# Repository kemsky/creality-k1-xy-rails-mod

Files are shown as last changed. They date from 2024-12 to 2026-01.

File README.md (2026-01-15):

# Creality `K1` XY Rails Mod

## Description

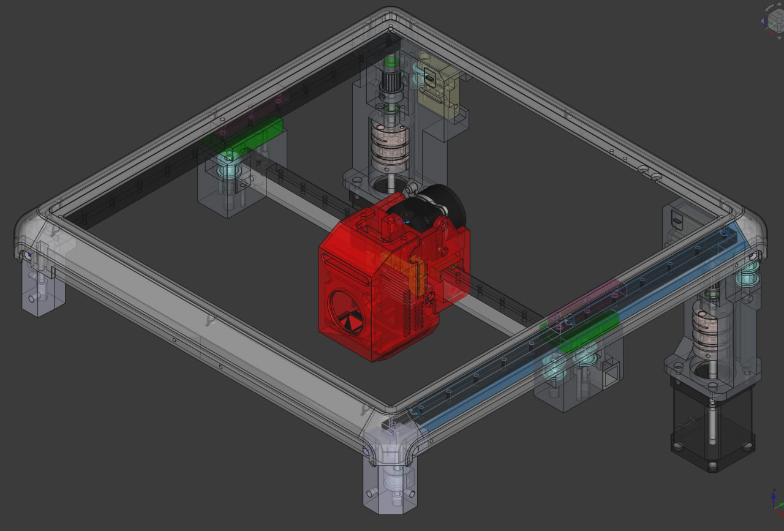
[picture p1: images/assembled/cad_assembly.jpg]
CAD


This mod fixes `K1` issues namely excessive ringing/echo, unstable print quality, frequent maintenance, also it makes printer quiet.

It should be compatible with regular `K1` (tested), `K1C` and `K1 SE` (not tested, likely heat sink needs to be replaced with heatsink from regular `K1`).

- **This mod does not change print area**
- **You must use camera mount from this mod (8mm lower than original)**
- **You must remove stock motor pulleys (or use non-stock stepper motors)**

### Belts, pulleys, motors

This mode uses `POWGE` 7.7 mm belt and corresponding idler pulleys. You can use 6 mm belt and stock idlers if you add washers to compensate height differences (`POWGE` idlers have 10.4 mm height). Also, you can use `F604ZZ` flanged bearings (4x12x4) and 2mm washers instead of `POWGE` pulleys.

You have to remove stock motor pulleys. You can use a bearing puller to do that (some people use printed pullers e.g. [pulley puller](https://www.printables.com/model/515503-pulley-puller)). If pulleys sit too tight you can use dremel and make cuts to relax pulleys. you have to be careful to avoid damage to motor shafts

I used 20T motor pulleys for 15 mm belt (`rotation_distance` needs to be adjusted to `40` and `driver_SGTHRS` must be tuned `printer.cfg`).

You can install non-stock motors e.g. `Leadshine 42cm06 1.8` (low VFA, need custom wiring, expensive) or `LDO-42STH48-1684MAC 0.9` (requires `full_steps_per_rotation: 400`, loud, limited acceleration, low VFA).

This mod uses double diaphragm couplers and `MF95ZZ` bearings.

#### Belts tuning

Preferred way is to use Spectroid android app (or any other program that can show sound frequency).

Move toolhead to the middle, move X axis to have 150mm between motor mounts and XY joints.

Pluck the shortest belt on each side, displayed frequency should be the same. Target frequency is 120-130Hz, if you go higher than 130Hz you risk to damage belts.

#### Linear rails

This mod uses two `MGN12` rails with `MGN12H` carriages for Y and one `MGN9` rail with `MGN9H` carriage for X axis.

X rail has max length of 331 mm, 300 mm between far left and far right holes. X axis requires 15x15x2 mm aluminium tube (the same length as rail). It is important to use quality rails for X axis (with minimal backlash).

Y rails have max length of 314 mm (safe 310 mm), 300 mm between far left and far right holes.

#### Materials

Recommended printing materials are PA-GF, PA-CF, ABS-GF, ABS-CF or anything else that is rigid and can sustain high temperatures. I don't recommend printing toolhead with pure ABS. I'd recommend PA-GF or PA-CF, as screw joints tend to become loose in ABS.

Wall loops, top/bottom layers should be at least 5, for motor mounts I'd recommend 6-7.

<details>
    <summary>Printing orientation</summary>
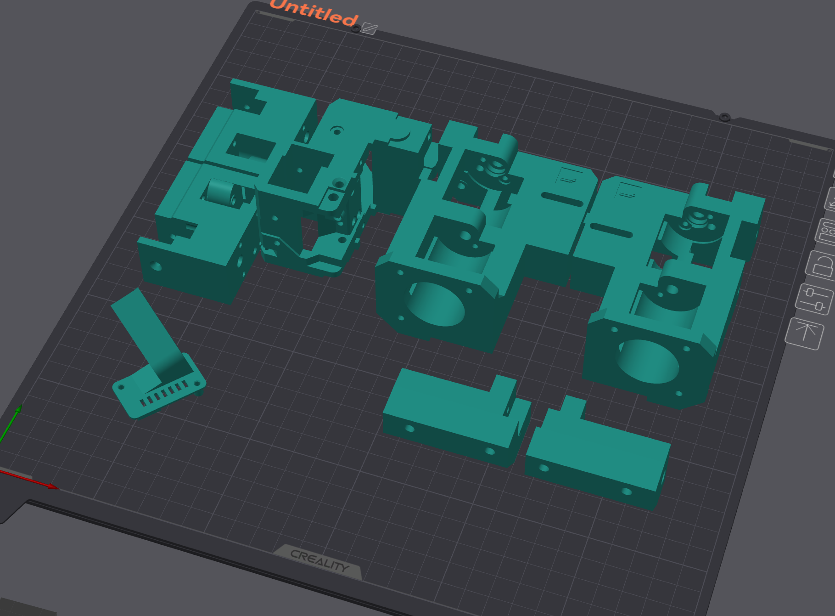
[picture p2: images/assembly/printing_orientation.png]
    
</details>

#### Options for maximum performance

- Use light extruder - [KKm extruder](https://www.printables.com/model/906070-artis3d-kkm-extruder-remix) (probably I'll upload my own remix)
- Use light extruder motor - LDO 36STH17-0354AHG or 36STH20-1004AHG
- Use light mgn9 rails - hollow/milled rails from FYSETC (they have 6mm height instead of 6.5mm, you have to print spacer)

## License

All work in this repository falls under the Attribution-NonCommercial-ShareAlike 4.0 International (CC BY-NC-SA 4.0).

<https://creativecommons.org/licenses/by-nc-sa/4.0/>

### Notes

Partially this work is based on [creality-k1-max-xy-rails-mod](https://github.com/kemsky/creality-k1-max-xy-rails-mod) and uses some CAD files made by [Henlor](https://www.printables.com/@Henlor).

## Published

<https://www.printables.com/model/1109686-creality-k1-xy-linear-rails-mod>

<https://www.thingiverse.com/thing:6893994>

<https://makerworld.com/en/models/931135>

## Photos

<details>
    <summary>Photo 1</summary>
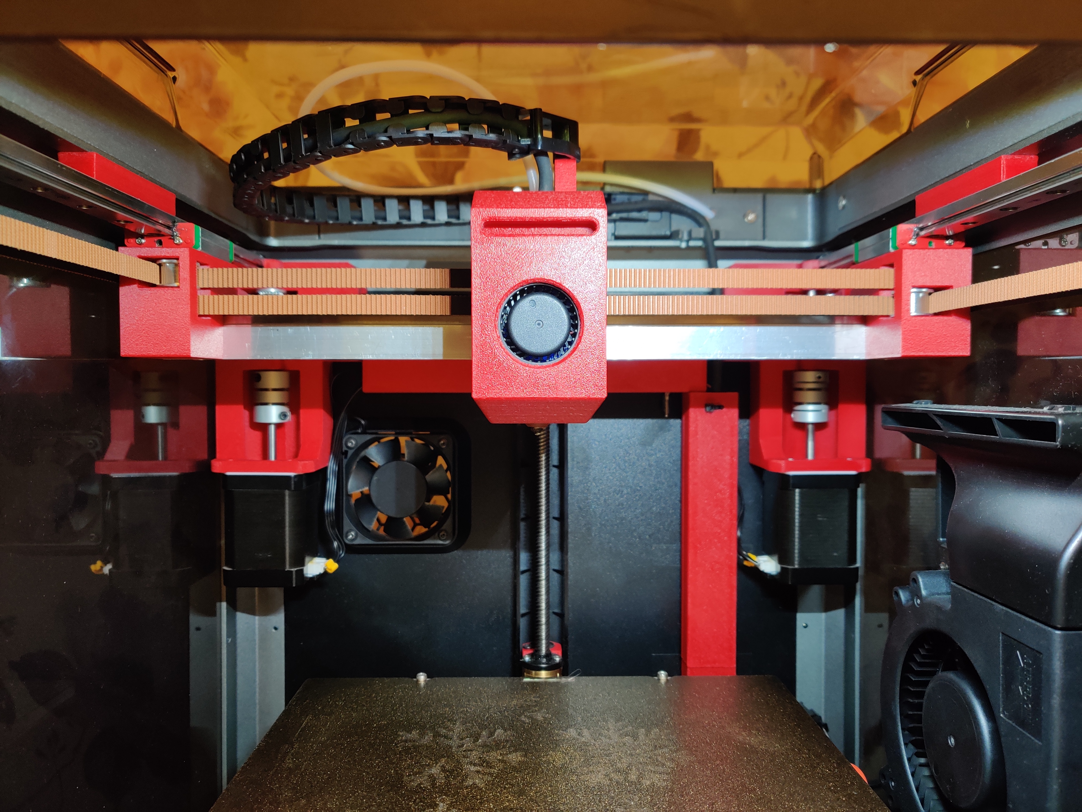
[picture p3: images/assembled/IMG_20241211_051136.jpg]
    
</details>

<details>
    <summary>Photo 2</summary>
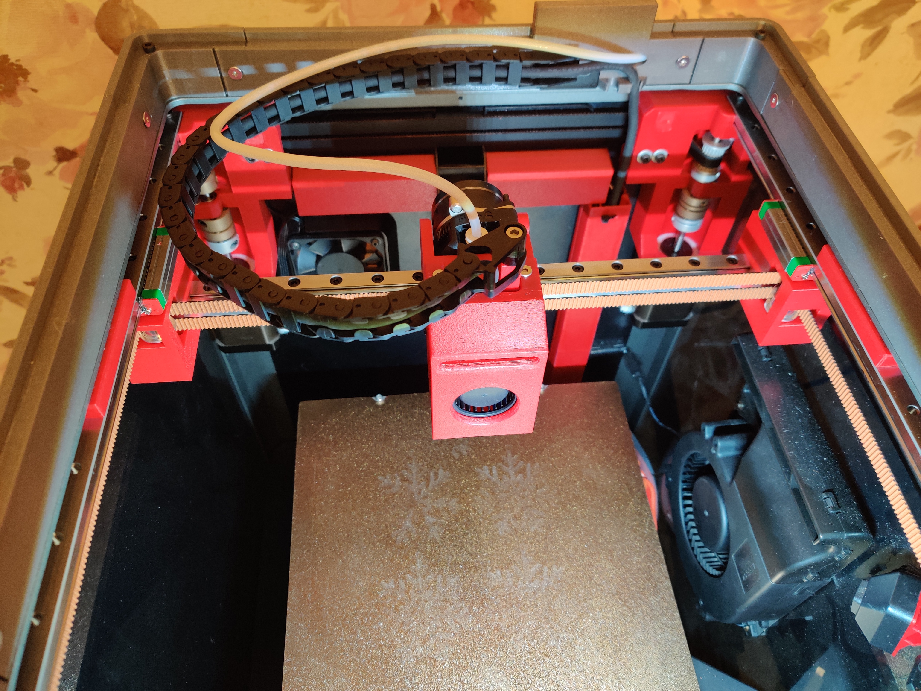
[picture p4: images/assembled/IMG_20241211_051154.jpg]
    
</details>

<details>
    <summary>Photo 3</summary>
    
</details>

<details>
    <summary>Photo 4</summary>
    
</details>

<details>
    <summary>Photo 5</summary>
    
</details>

## BOM, Assembly

! `Flat Thin Wafer Head Screw` - M3 screws with flat head that has 1 mm thickness.
You can find those on AliExpress, manufacturer NINDEJIN, search for "Ultra Low Profile Head Screw".

### Camera

<details>
    <summary>Preview</summary>
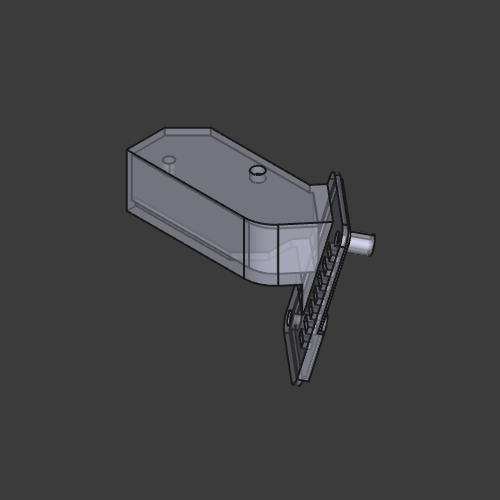
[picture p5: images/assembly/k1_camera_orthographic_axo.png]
k1_camera.stl
    
</details>
<br>

[k1_camera.stl](/stl/k1_camera.stl)

### Front idler left

<details>
    <summary>Preview</summary>
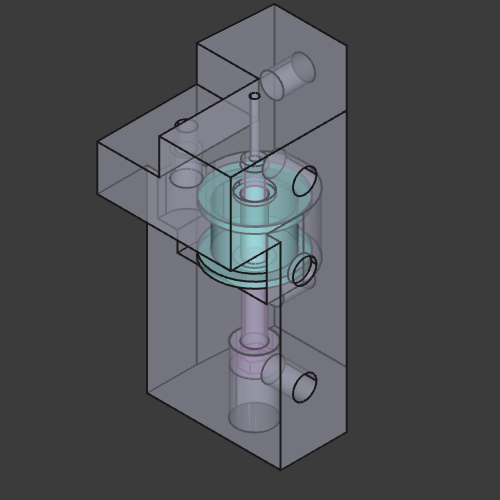
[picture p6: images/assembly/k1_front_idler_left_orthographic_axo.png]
front_idler_left.stl
    
</details>
<br>

[front_idler_left.stl](/stl/k1_front_idler_left.stl)

| Item | Type | Count |
|---|---|---|
| DIN 912 Socket Head Cap Screw | M4 30 mm  | 1 |
| DIN 7991 Flat Head Cap Screw | M3 6 mm | 4 |
| DIN 912 Socket Head Cap Screw | M3 16 mm  | 1 |
| POWGE GT2 No Teeth Idler Pulley | 7.7 mm | 1 |
| Heat insert | M3 5x5 mm | 5 |

### Front idler right

<details>
    <summary>Preview</summary>
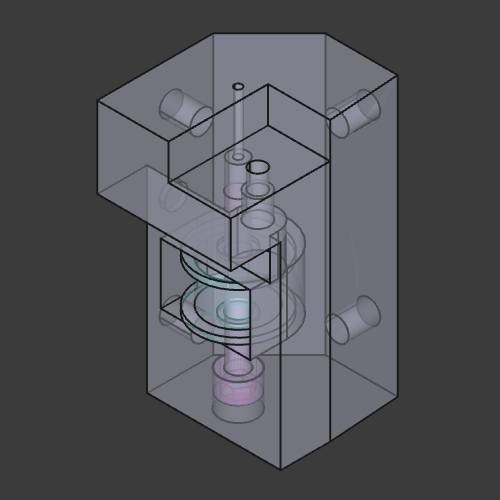
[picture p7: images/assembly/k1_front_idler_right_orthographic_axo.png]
front_idler_right.stl
    
</details>
<br>

[front_idler_right.stl](/stl/k1_front_idler_right.stl)

| Item | Type | Count |
|---|---|---|
| DIN 912 Socket Head Cap Screw | M4 30 mm  | 1 |
| DIN 7991 Flat Head Cap Screw | M3 6 mm | 4 |
| DIN 912 Socket Head Cap Screw | M3 16 mm  | 1 |
| POWGE GT2 No Teeth Idler Pulley | 7.7 mm | 1 |
| Heat insert | M3 5x5 mm | 5 |

### Joint left

<details>
    <summary>Preview</summary>
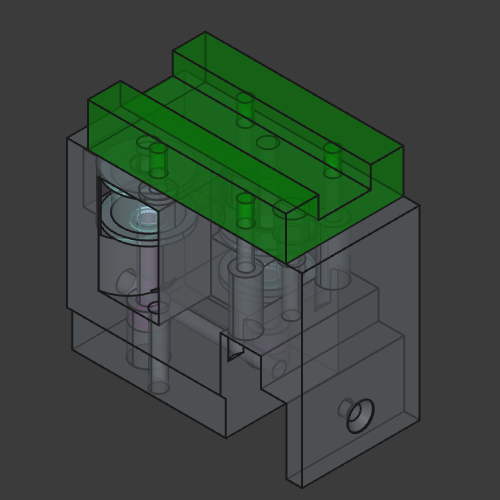
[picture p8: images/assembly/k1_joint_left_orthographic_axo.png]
k1_joint_left.stl
    
</details>
<br>

[k1_joint_left.stl](/stl/k1_joint_left.stl)

| Item | Type | Count |
|---|---|---|
| DIN 912 Socket Head Cap Screw | M4 30 mm | 2 |
| DIN 7991 Flat Head Cap Screw | M3 52 mm | 1 |
| Flat Thin Wafer Head Screw | M3 6 mm | 1 |
| DIN 912 Socket Head Cap Screw | M3 12 mm | 3 |
| DIN 912 Socket Head Cap Screw | M3 25 mm | 1 |
| POWGE GT2 No Teeth Idler Pulley | 7.7 mm | 2 |
| MGN12H block | | 1 |
| Heat insert | M3 4.5x5 mm | 1 |
| Heat insert | M3 5x7 mm | 1 |

### Joint right

<details>
    <summary>Preview</summary>
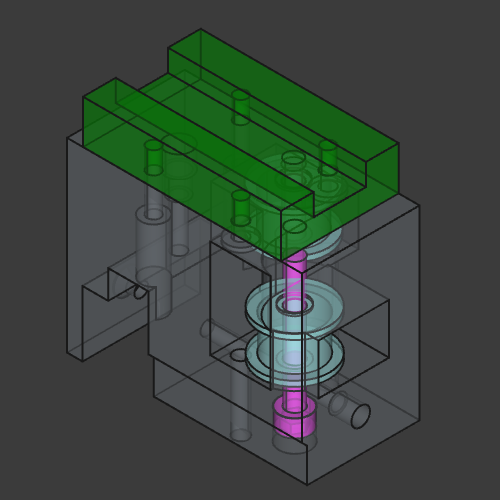
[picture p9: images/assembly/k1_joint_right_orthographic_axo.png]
k1_joint_right.stl
    
</details>
<br>

[k1_joint_right.stl](/stl/k1_joint_right.stl)

| Item | Type | Count |
|---|---|---|
| DIN 912 Socket Head Cap Screw | M4 30 mm | 2 |
| DIN 7991 Flat Head Cap Screw | M3 52 mm | 1 |
| Flat Thin Wafer Head Screw | M3 6 mm | 2 |
| DIN 912 Socket Head Cap Screw | M3 12 mm | 2 |
| DIN 912 Socket Head Cap Screw | M3 25 mm | 1 |
| POWGE GT2 No Teeth Idler Pulley | 7.7 mm | 2 |
| MGN12H block | | 1 |
| Heat insert | M3 4.5x5 mm | 1 |
| Heat insert | M3 5x7 mm | 1 |

### Y rail mounts

<details>
    <summary>Preview</summary>
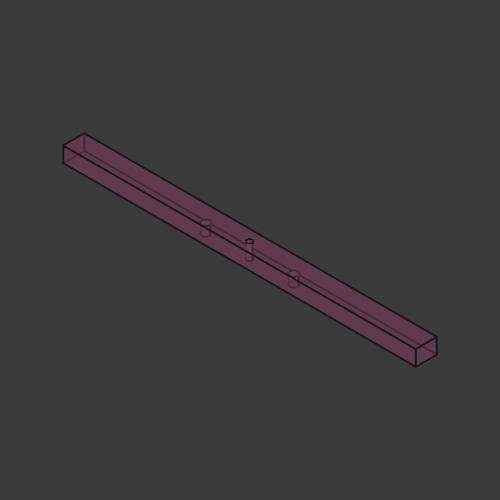
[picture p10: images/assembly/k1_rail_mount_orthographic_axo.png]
k1_rail_mount.stl
    
</details>
<br>

[k1_rail_mount.stl](/stl/k1_rail_mount.stl) x2

| Item | Type | Count |
|---|---|---|
| DIN 912 Socket Head Cap Screw | M3 16 mm  | 1 |
| DIN 912 Socket Head Cap Screw | M3 8 mm | 2 |
| Heat insert | M3 5x5 mm | 2 |

Mounting Y rails to the top frame is important if you want less vibrations.
Default mount option is printed mount. You'll have to drill and tap M3 thread in the top frame.

Instead of printed mount you can buy metal plate or a set of plates to get ~8.5 mm thickness.

### Y axis

See [cad_rail_mgn12.FCStd](/src/cad_rail_mgn12.FCStd) for exact configuration and dimensions.

| Item | Type | Count |
|---|---|---|
| MGN12 liner rail | 310 mm | 2 |

### X axis

See [cad_x_axis.FCStd](/src/cad_x_axis.FCStd) for exact configuration and dimensions.

First, make two holes on the left and on the right, tap M3 threads, mount MGN9 rail, align it carefully and tighten screws. Use rail as drilling template, first make mark using 4 mm drill bit, then drill remaining holes using 2.5 mm drill bit, then tap M3 threads.

| Item | Type | Count |
|---|---|---|
| Aluminium square pipe | 15x15x2 331 mm | 1 |
| DIN 912 Socket Head Cap Screw | M3 6 mm | 7-14  |
| MGN9 liner rail | 331 mm | 1 |

### Tensioner left

<details>
    <summary>Preview</summary>
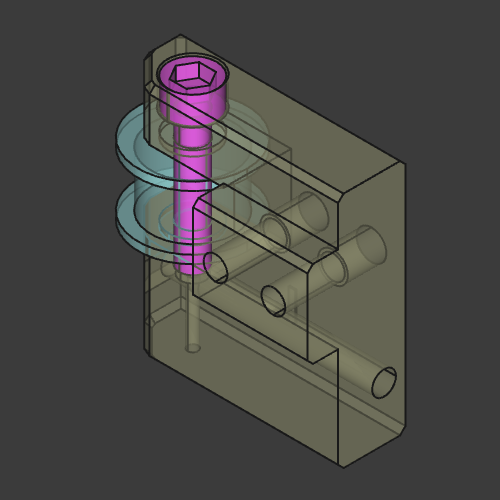
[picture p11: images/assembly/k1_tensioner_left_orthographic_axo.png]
k1_tensioner_left.stl
    
</details>
<br>

[k1_tensioner_left.stl](/stl/k1_tensioner_left.stl)

| Item | Type | Count |
|---|---|---|
| DIN 912 Socket Head Cap Screw | M3 45 mm | 1 |
| DIN 912 Socket Head Cap Screw | M3 16 mm | 2 |
| DIN 912 Socket Head Cap Screw | M4 20 mm | 1 |
| Washer/Gasket | M3 | 2 |
| POWGE GT2 No Teeth Idler Pulley | 7.7 mm | 1 |
| Heat insert | M3 3x4.5 mm | 2 |

### Tensioner right

<details>
    <summary>Preview</summary>
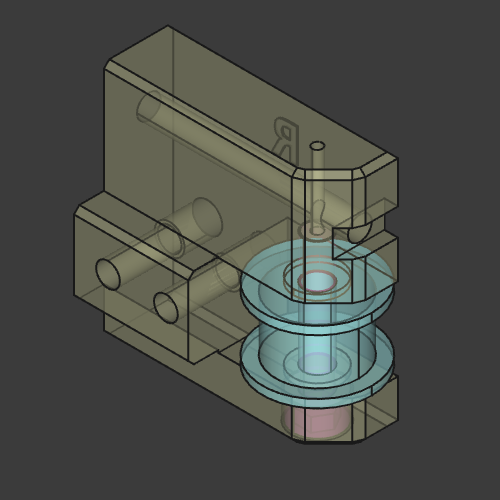
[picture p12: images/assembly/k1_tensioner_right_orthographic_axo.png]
k1_tensioner_right.stl
    
</details>
<br>

[k1_tensioner_right.stl](/stl/k1_tensioner_right.stl)

| Item | Type | Count |
|---|---|---|
| DIN 912 Socket Head Cap Screw | M3 45 mm | 1 |
| DIN 912 Socket Head Cap Screw | M3 16 mm | 2 |
| DIN 912 Socket Head Cap Screw | M4 20 mm | 1 |
| Washer/Gasket | M3 | 2 |
| POWGE GT2 No Teeth Idler Pulley | 7.7 mm | 1 |
| Heat insert | M3 3x4.5 mm | 2 |

### Motor mount left

<details>
    <summary>Preview</summary>
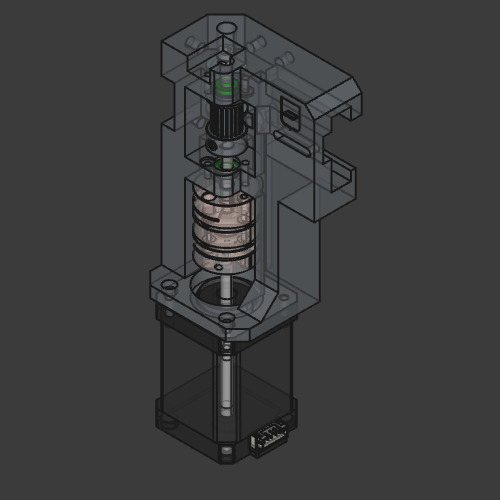
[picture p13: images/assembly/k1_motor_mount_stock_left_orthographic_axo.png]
k1_motor_mount_stock_left.stl
    
</details>
<br>

- For stock motors - [k1_motor_mount_stock_left.stl](/stl/k1_motor_mount_stock_left.stl)
- For non-stock motors - [k1_motor_mount_left.stl](/stl/k1_motor_mount_left.stl)

| Item | Type | Count |
|---|---|---|
| DIN 7991 Flat Head Cap Screw | M3 6 mm | 4 |
| DIN 912 Socket Head Cap Screw | M3 6 mm | 3 |
| DIN 912 Socket Head Cap Screw | M3 16 mm  | 1 |
| Flat Thin Wafer Head Screw | M3 6 mm | 2 |
| MF95ZZ Bearing | | 2 |
| Double Diaphragm Coupler | 20x30 5x5 | 1 |
| Shaft | 5x57 mm | 1 |
| Motor Pulley for 15mm belt | 20T 5 mm  | 1 |
| POWGE GT2 No Teeth Idler Pulley | 7.7 mm | 2 |
| Heat insert | M3 5x5 mm | 6 |

You'll need 1 M3x35 screw from stock gantry motor mounts.

### Motor mount right

<details>
    <summary>Preview</summary>
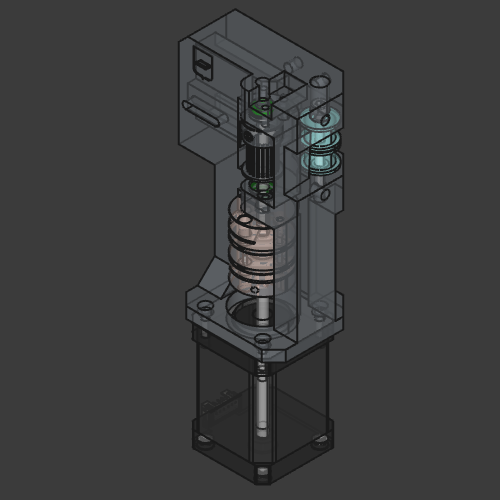
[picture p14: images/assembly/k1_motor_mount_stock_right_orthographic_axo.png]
k1_motor_mount_stock_right.stl
    
</details>
<br>

- For stock motors - [k1_motor_mount_stock_right.stl](/stl/k1_motor_mount_stock_right.stl)
- For non-stock motors - [k1_motor_mount_right.stl](/stl/k1_motor_mount_right.stl)

| Item | Type | Count |
|---|---|---|
| DIN 7991 Flat Head Cap Screw | M3 6 mm | 4 |
| DIN 912 Socket Head Cap Screw | M3 6 mm | 3 |
| DIN 912 Socket Head Cap Screw | M3 16 mm  | 1 |
| Flat Thin Wafer Head Screw | M3 6 mm | 2 |
| MF95ZZ Bearing | | 2 |
| Double Diaphragm Coupler | 20x30 5x5 | 1 |
| Shaft | 5x57 mm | 1 |
| Motor Pulley for 15mm belt | 20T 5 mm  | 1 |
| POWGE GT2 No Teeth Idler Pulley | 7.7 mm | 2 |
| Heat insert | M3 5x5 mm | 6 |

You'll need 1 M3x35 screw from stock gantry motor mounts.

### Toolhead clamp left

<details>
    <summary>Preview</summary>
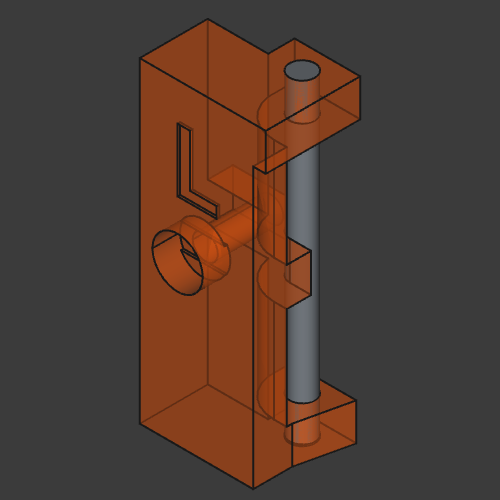
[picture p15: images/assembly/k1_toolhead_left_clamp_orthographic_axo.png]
k1_toolhead_left_clamp.stl
    
</details>
<br>

[k1_toolhead_left_clamp.stl](/stl/k1_toolhead_left_clamp.stl)

| Item | Type | Count |
|---|---|---|
| DIN 912 Socket Head Cap Screw | M2 10 mm | 1 |
| Shaft | 2x25 mm | 1 |

### Toolhead clamp right

<details>
    <summary>Preview</summary>
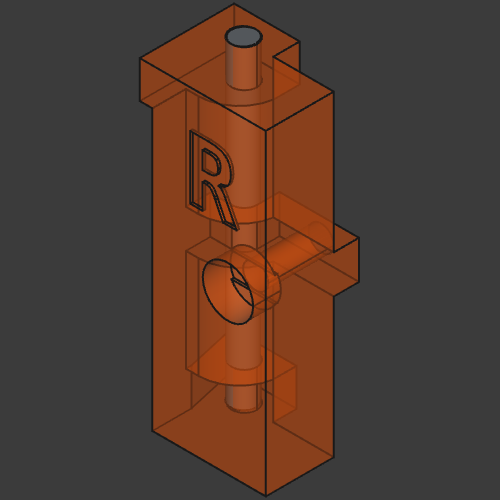
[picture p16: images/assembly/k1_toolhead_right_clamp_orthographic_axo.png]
k1_toolhead_right_clamp.stl
    
</details>
<br>

[k1_toolhead_right_clamp.stl](/stl/k1_toolhead_right_clamp.stl)

| Item | Type | Count |
|---|---|---|
| DIN 912 Socket Head Cap Screw | M2 10 mm | 1 |
| Shaft | 2x25 mm | 1 |

### Toolhead fan spacer

<details>
    <summary>Preview</summary>
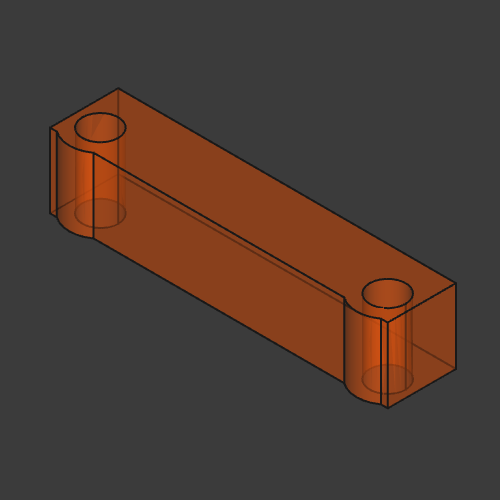
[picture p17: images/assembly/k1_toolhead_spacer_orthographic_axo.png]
k1_toolhead_spacer.stl
    
</details>
<br>

Regular hotend - [k1_toolhead_spacer.stl](/stl/k1_toolhead_spacer.stl)

Unicorn hotend - [k1_toolhead_spacer_unicorn.stl](/stl/k1_toolhead_spacer_unicorn.stl)

### Toolhead

<details>
    <summary>Preview</summary>
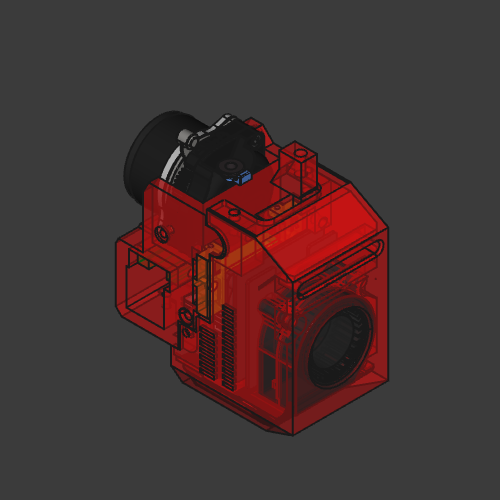
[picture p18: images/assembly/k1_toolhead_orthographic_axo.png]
k1_toolhead.stl
    
</details>
<br>

[k1_toolhead.stl](/stl/k1_toolhead.stl)

| Item | Type | Count |
|---|---|---|
| Flat Thin Wafer Head Screw | M3 6 mm | 4 |
| Flat Thin Wafer Head Screw | M3 8 mm | 3 |
| DIN 912 Socket Head Cap Screw | M2 12 mm | 1 |
| MGN9H block | | 1 |
| Heat insert | M3 4.5x3 mm | 6 |
| Heat insert | M3 5x7 mm | 1 |
| Heat insert | M3 5x4 mm | 4 |
| Heat insert | M2 3.5x3 mm | 4 |

#### Toolhead Microprobe

| Item | Type | Count |
|---|---|---|
| Heat insert | M2.5 3.5x4 mm | 2 |

You can install `BIQU MicroProbe` sensor which is much better than original load cell probe.

[ **!** ] Pins on toolhead board ("touch" connector) do not match microprobe pins, you can not use premade JST 1.25 5pins cable, you'll have to make your own.

<details>
    <summary>Pins</summary>
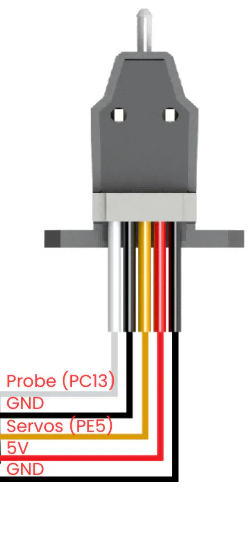
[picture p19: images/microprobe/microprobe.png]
microprobe
    
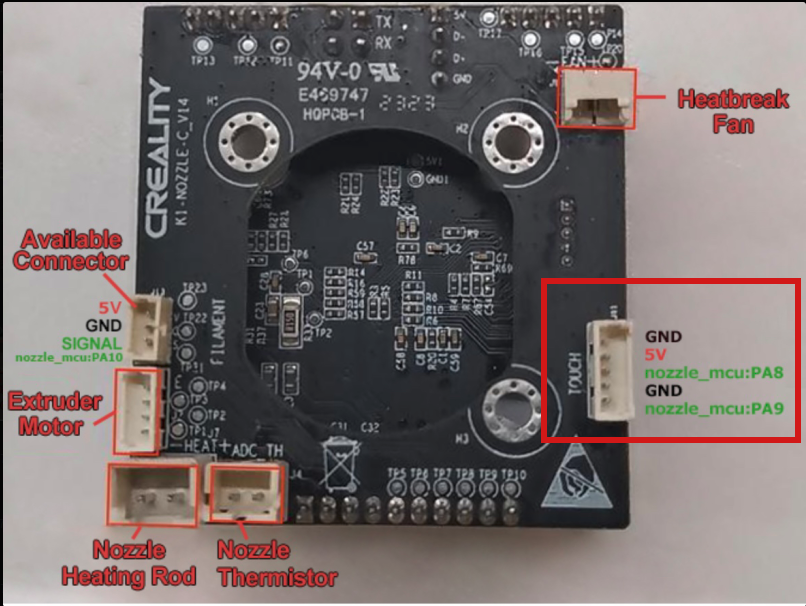
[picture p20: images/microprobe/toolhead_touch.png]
toolhead_touch
    
</details>
<br>

```pre
- touch GND            -> microprobe GND    (black)
- touch 5v             -> microprobe 5v     (red)
- touch nozzle_mcu:PA8 -> microprobe servo  (yellow)
- touch GND            -> microprobe GND    (black)
- touch nozzle_mcu:PA9 -> microprobe probe  (white)
```

1. Remove all `prtouch` sections from `printer.cfg`
2. Edit `/usr/share/klipper/klippy/extras/custom_macro.py` and comment all prtouch usages
3. Remove `/usr/share/klipper/klippy/extras/custom_macro.pyc` and reboot
4. Add the following to `printer.cfg`:

    ```cfg
    [gcode_macro _PROBE_DOWN]
    gcode:
        SET_PIN PIN=probe_enable VALUE=1

    [gcode_macro _PROBE_UP]
    gcode:
        SET_PIN PIN=probe_enable VALUE=0

    [output_pin probe_enable]
    pin: nozzle_mcu:PA8
    value: 0

    [probe]
    pin: ^!nozzle_mcu:PA9
    deactivate_on_each_sample: False
    x_offset: 0
    y_offset: 20
    z_offset: 0  # do PROBE_CALIBRATE
    samples: 2
    samples_tolerance: 0.05
    samples_tolerance_retries: 3
    activate_gcode:
        _PROBE_DOWN
        G4 P500
    deactivate_gcode:
        _PROBE_UP
    ```

5. Modify `[stepper_z]` section in `printer.cfg`, set `endstop_pin` to `probe:z_virtual_endstop`
6. Use `PROBE_CALIBRATE` macros to determine Z-Offset and save it.
7. Sometimes you can get error `Communication Timeout during homing z`. Use `vi /usr/share/klipper/klippy/mcu.py` and increase `TRSYNC_TIMEOUT` from 0.025 up to 0.05. Remove file `/usr/share/klipper/klippy/mcu.pyc`, reboot.

Depending on your hotend you may need a spacer.

<details>
    <summary>Microprobe spacer</summary>
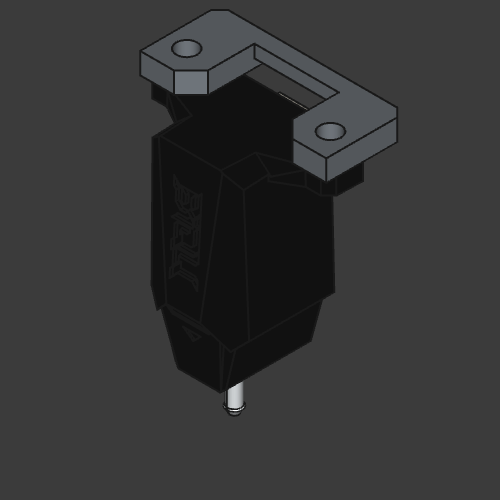
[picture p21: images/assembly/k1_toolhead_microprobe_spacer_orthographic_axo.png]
k1_toolhead_microprobe_spacer.stl
    
</details>
<br>

[k1_toolhead_microprobe_spacer.stl](/stl/k1_toolhead_microprobe_spacer.stl)

## Bonus Models

### Toolhead cover

<details>
    <summary>Preview</summary>
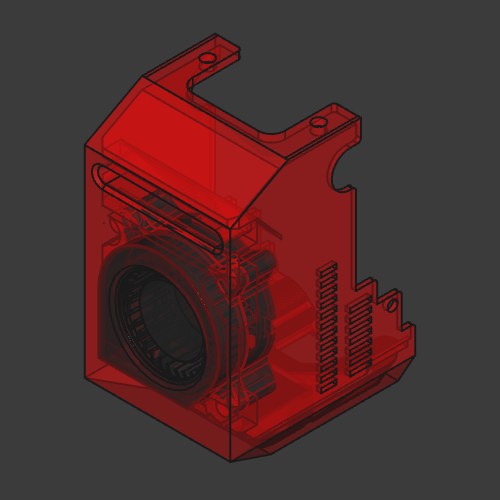
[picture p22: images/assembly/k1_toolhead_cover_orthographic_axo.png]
k1_toolhead_cover.stl
    
</details>
<br>

[k1_toolhead_cover.stl](/stl/k1_toolhead_cover.stl)

### Compact toolhead cover

<details>
    <summary>Preview</summary>
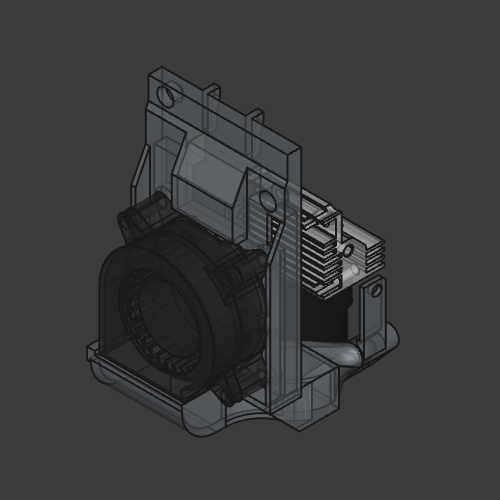
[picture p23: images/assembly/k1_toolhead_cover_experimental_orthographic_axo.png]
k1_toolhead_cover_experimental.stl
    
</details>
<br>

[k1_toolhead_cover_experimental.stl](/stl/k1_toolhead_cover_experimental.stl)

### Cable covers

<details>
    <summary>Preview</summary>
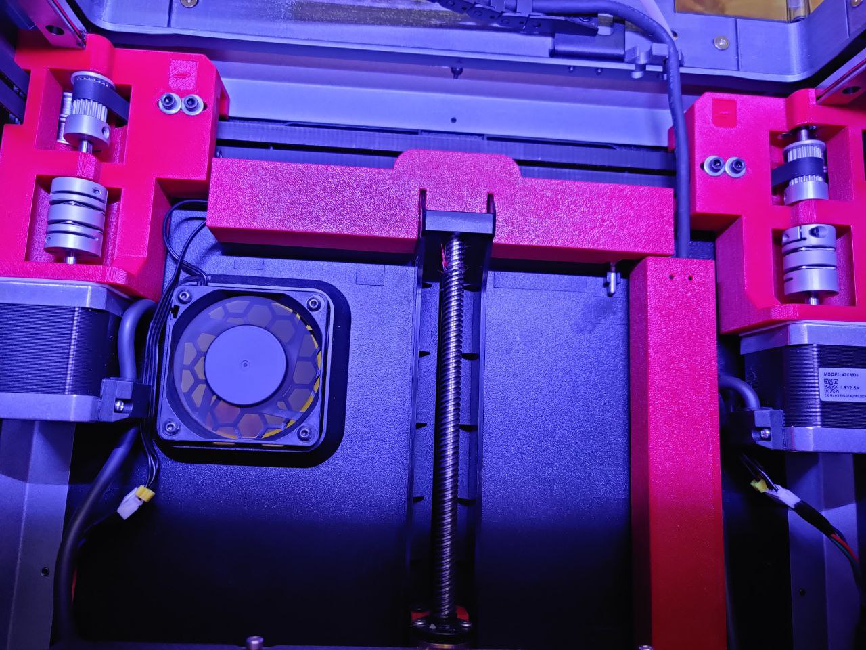
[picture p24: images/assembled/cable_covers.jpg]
cable covers
    
</details>
<br>

Horizontal - [k1_cable_cover_horizontal.stl](/stl/k1_cable_cover_horizontal.stl)

Vertical top - [k1_cable_cover_vertical_top.stl](/stl/k1_cable_cover_vertical_top.stl)

Vertical bottom - [k1_cable_cover_vertical_bottom.stl](/stl/k1_cable_cover_vertical_bottom.stl)

### Z-Carriage for T8 Oldham Coupler

<details>
    <summary>Preview</summary>
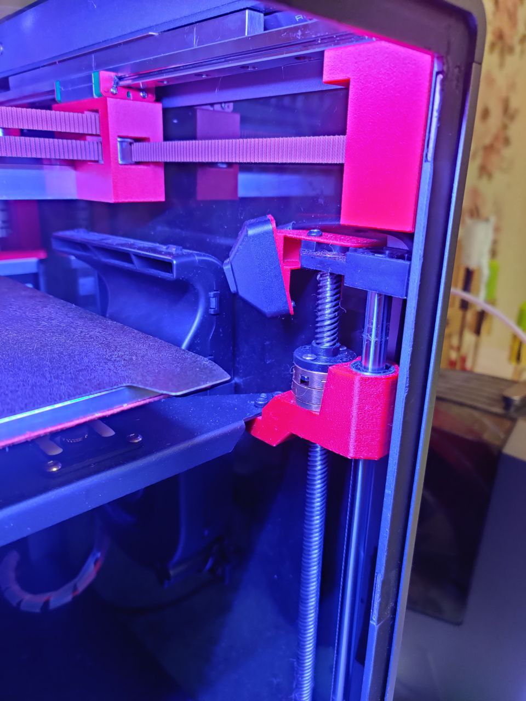
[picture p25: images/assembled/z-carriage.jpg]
k1_z_carriage_oldham.stl
    
</details>
<br>

[k1_z_carriage_oldham.stl](/stl/k1_z_carriage_oldham.stl)

### Side fan duct

<details>
    <summary>Preview</summary>
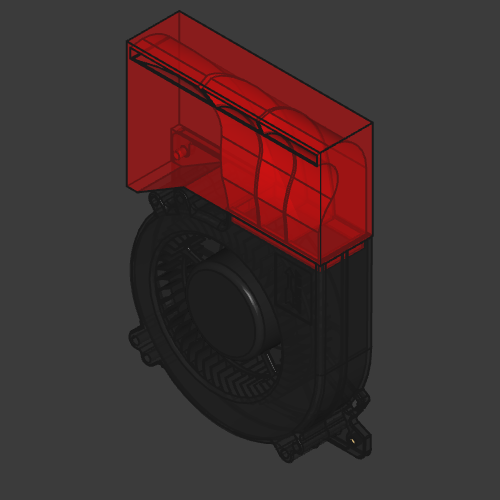
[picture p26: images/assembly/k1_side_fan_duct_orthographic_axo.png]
k1_side_fan_duct.stl
    
</details>
<br>

[k1_side_fan_duct.stl](/stl/k1_side_fan_duct.stl)

### Cutter block

Requires 2x25mm DIN 912 M3 screws.

<details>
    <summary>Preview</summary>
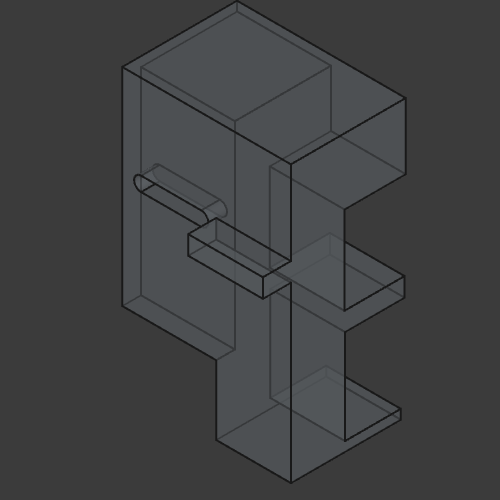
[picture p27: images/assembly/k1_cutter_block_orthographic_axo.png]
k1_side_fan_duct.stl k1_cutter_block.stl
    
</details>
<br>

[k1_cutter_block.stl](/stl/k1_cutter_block.stl)

## Automation

`export.sh`/`export.cmd` scripts export all necessary objects to STl and STEP and optionally capture model screenshots.

```bash
# without updating screenshots:
./export.sh
# export STL, STEP and generate model screenshots:
./export.sh screenshots
```

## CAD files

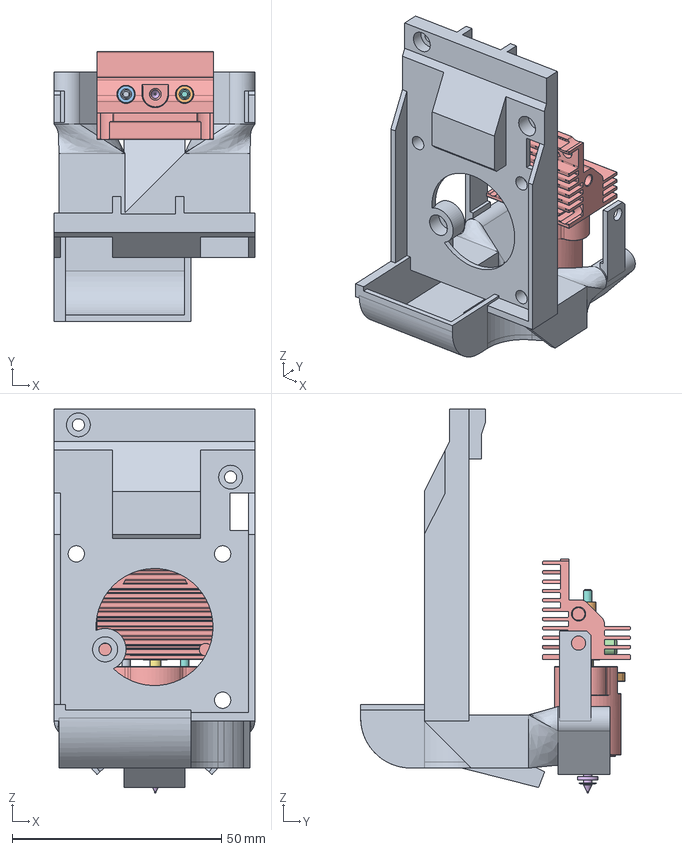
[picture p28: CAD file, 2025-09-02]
src/k1_toolhead_cover_experimental.FCStd
48.0 x 64.5 x 91.9 mm
k1_toolhead_cover_experimental
ceramic-heater-mount
ceramic-heater-main-body
ceramic-heater-ring
Silicone Socks
K1-nozzle
Heat-brake
M2 x 22 mm SBHC
M2 x 22 mm SBHC001
PTFE tubes
PTFE tubes001
M4 x 4mm grub screw

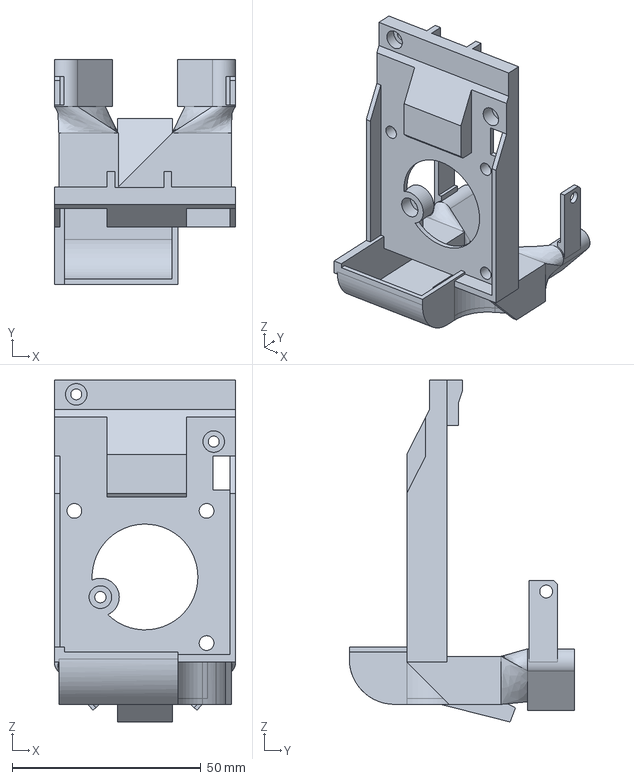
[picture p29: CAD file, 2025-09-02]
step/k1_toolhead_cover_experimental.step
48.0 x 59.7 x 90.5 mm

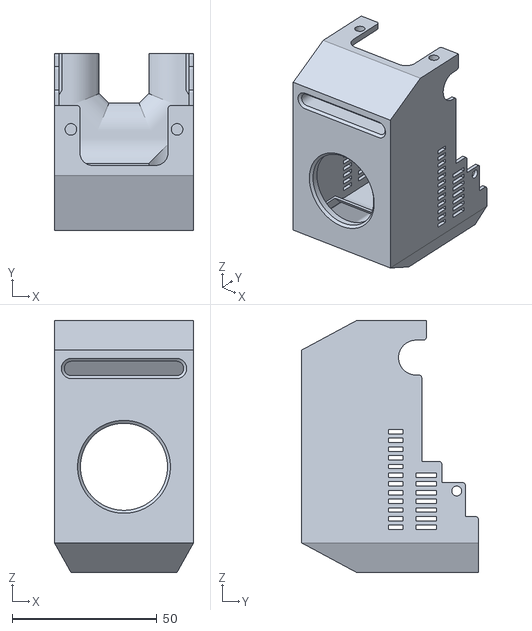
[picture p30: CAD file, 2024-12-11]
stl/k1_toolhead_cover.stl
48.0 x 61.0 x 86.9

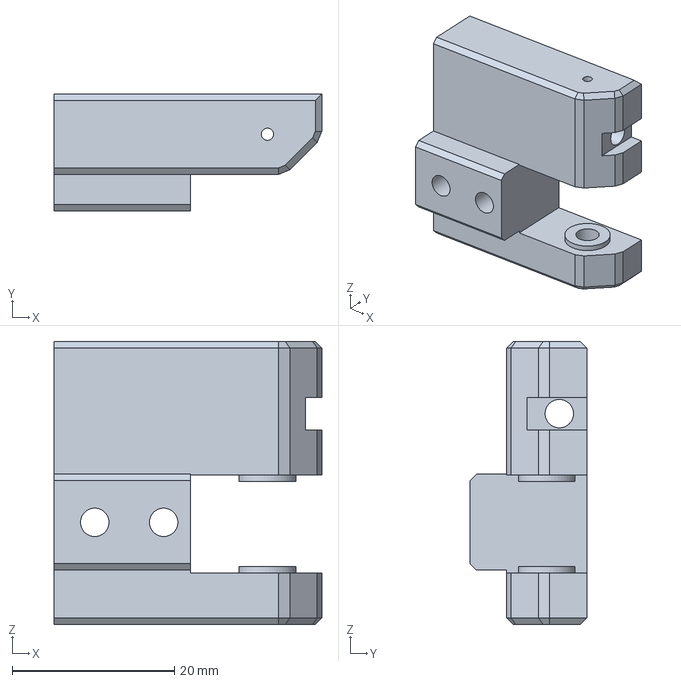
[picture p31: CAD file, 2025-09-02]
src/k1_tensioner_right.FCStd
33.0 x 14.4 x 34.9 mm

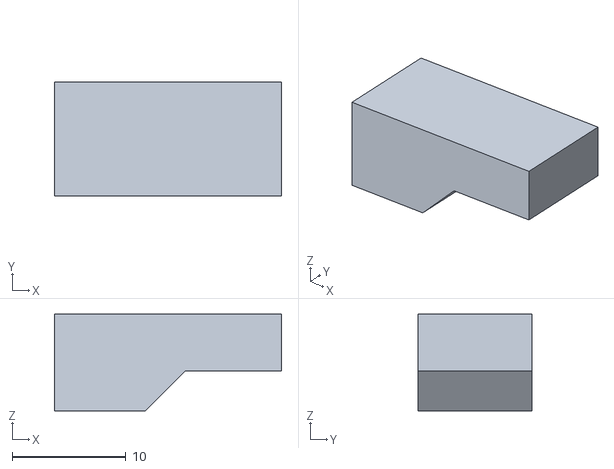
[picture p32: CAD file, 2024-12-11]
stl/tool_print_test.stl
20.0 x 10.0 x 8.54

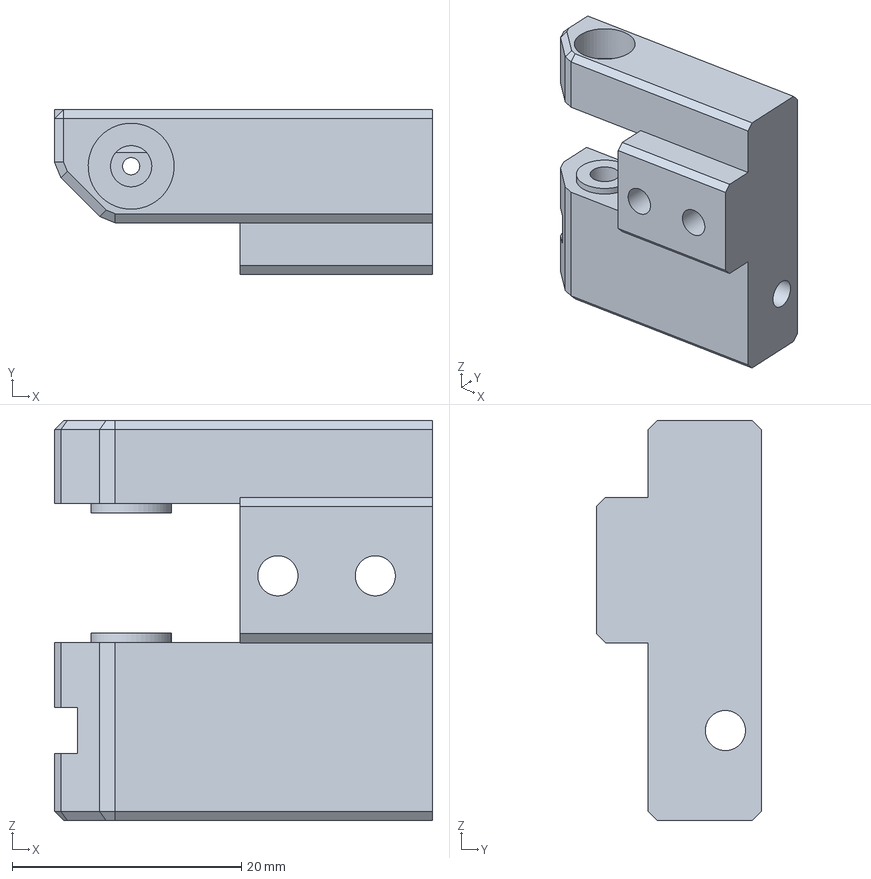
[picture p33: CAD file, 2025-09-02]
src/k1_tensioner_left.FCStd
33.0 x 14.4 x 34.9 mm

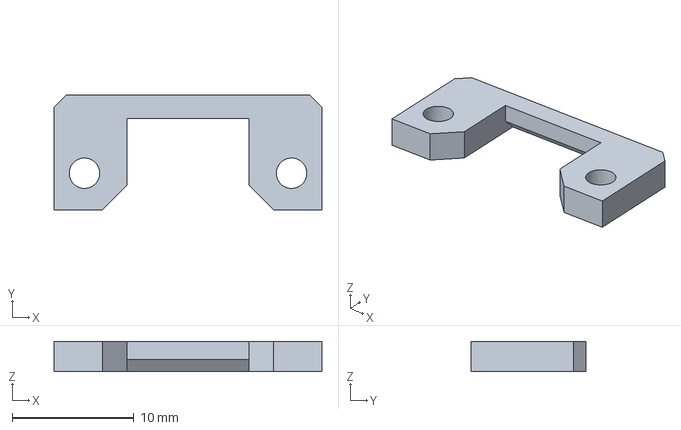
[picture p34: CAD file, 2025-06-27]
step/k1_toolhead_microprobe_spacer.step
22.0 x 9.40 x 2.50 mm

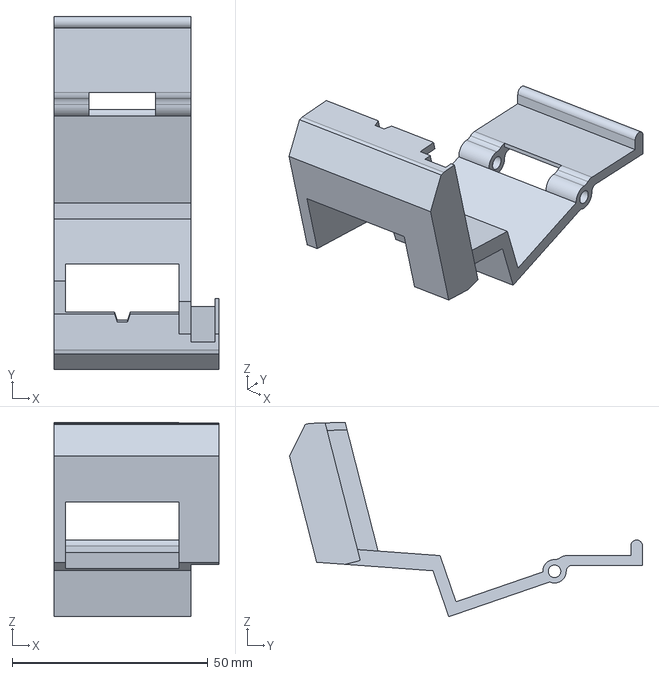
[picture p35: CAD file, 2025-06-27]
src/k1_hopper.FCStd
42.2 x 90.3 x 49.7 mm

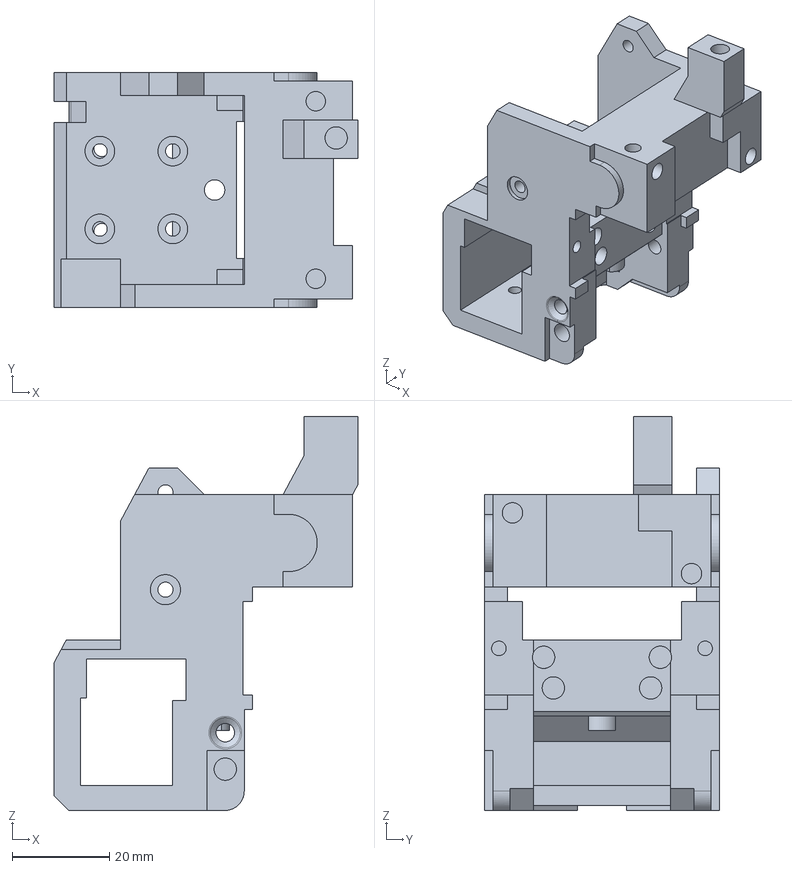
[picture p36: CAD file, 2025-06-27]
step/k1_toolhead.step
62.4 x 48.4 x 81.0 mm

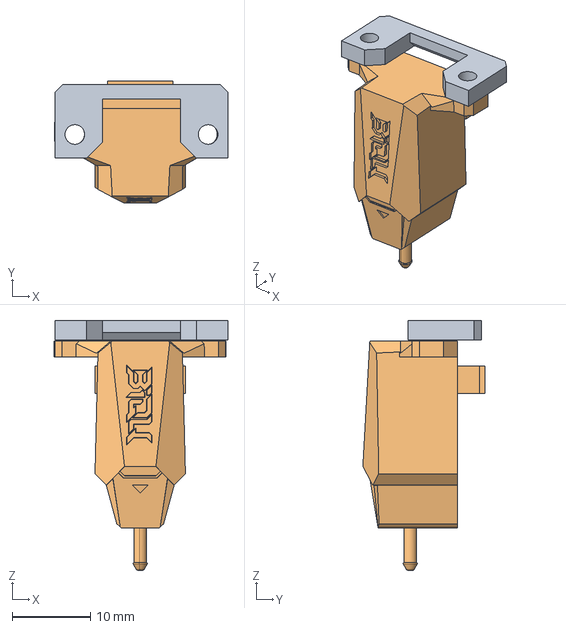
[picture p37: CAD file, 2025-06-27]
src/k1_toolhead_microprobe_spacer.FCStd
22.1 x 15.6 x 31.9 mm
k1_toolhead_microprobe_spacer
BIQU microprobe mockup

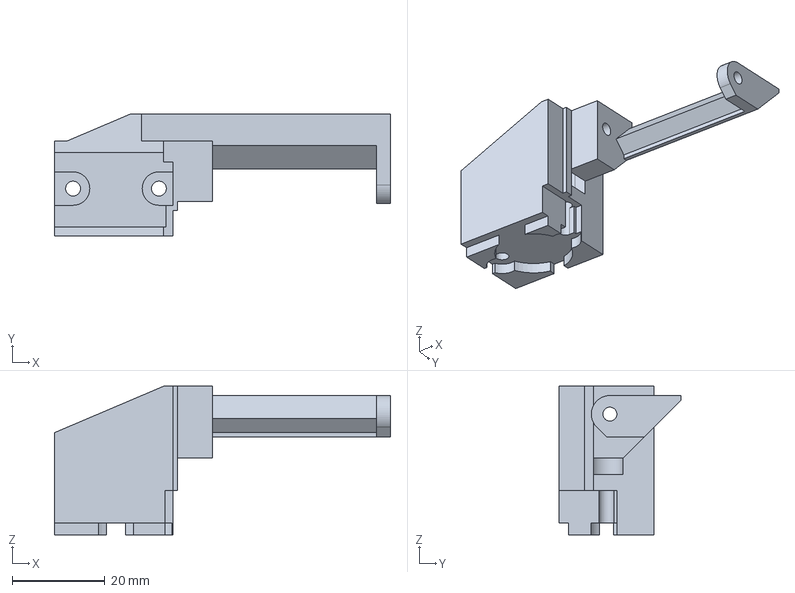
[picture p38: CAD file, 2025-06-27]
step/k1_hopper_fixed_block.step
72.4 x 26.4 x 32.0 mm

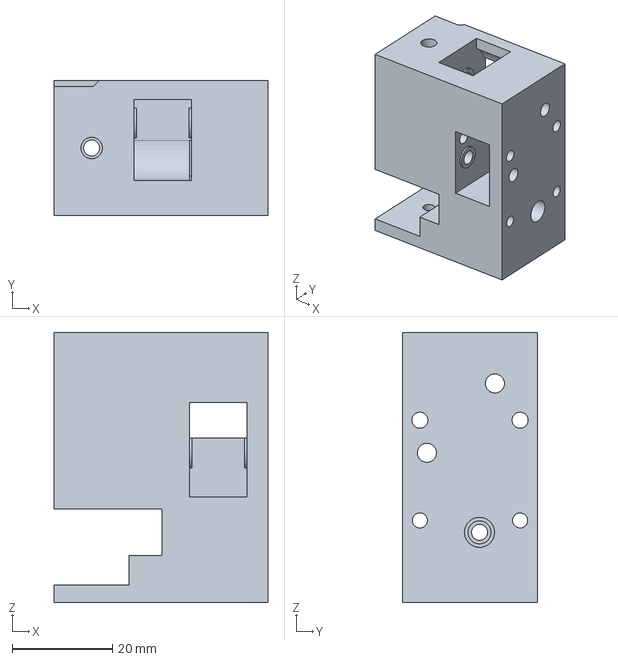
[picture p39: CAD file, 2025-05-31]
step/k1_joint_right.step
42.7 x 27.0 x 53.9 mm

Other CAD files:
src/cad_assembly.FCStd
step/k1_tensioner_right.step
src/k1_toolhead.FCStd
step/k1_hopper.step
src/k1_hopper_fixed_block.FCStd
src/k1_joint_left.FCStd
src/cad_15x15.FCStd
src/cad_20T_15mm_pulley.FCStd
src/cad_3010.FCStd
src/cad_4020.FCStd
src/cad_M4_DIN912_20mm.FCStd
src/cad_M4_DIN912_30mm.FCStd
src/cad_diaphragm_coupler.FCStd
src/cad_hotend.FCStd
src/cad_m4_35mm.FCStd
src/cad_mf95zz.FCStd
src/cad_mgn12h_block.FCStd
src/cad_mgn9h_block.FCStd
src/cad_motor_shaft_55mm.FCStd
src/cad_nema17_42_48.FCStd
src/cad_nema17_42_60.FCStd
src/cad_pcb.FCStd
src/cad_powge_pulley.FCStd
src/cad_rail_mgn12.FCStd
src/cad_rail_mgn9.FCStd
src/cad_shaft_2_25mm.FCStd
src/cad_x_axis.FCStd
src/cad_x_gantry.FCStd
src/k1_cable_cover_horizontal.FCStd
src/k1_cable_cover_vertical_bottom.FCStd
src/k1_cable_cover_vertical_top.FCStd
src/k1_camera.FCStd
src/k1_cutter_block.FCStd
src/k1_front_idler_left.FCStd
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

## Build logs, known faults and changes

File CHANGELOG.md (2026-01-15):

# Changelog

## 2026-01-15

- BOM fix

## 2025-12-29

- update microprobe docs

## 2025-09-02

- correct tensioners size
- add microprobe fix

## 2025-06-28

- added printing orientation

## 2025-06-27

- added BIQU Microprobe option

## 2025-05-31

- added initial version of hopper
- modifled motor mounts to simplify bearings installation
- changed joints to use 52mm screws to make it more rigid

## 2025-05-03

- prepare motor mounts and toolhead for cfs

## 2025-04-20

- make toolhead compatible with extruder from Creality CFS kit

## 2025-04-04

- joints samll fixes
- remove experimental joints for teeth pulleys
- added L, R marks on clamps and tensioners
- updated assembly file

## 2025-03-25

- updated new toolhead cover

## 2025-03-05

- updated new toolhead cover
- experimental 2xmgn5 toolhead
- improved front idlers, joints

## 2025-02-05

- added new toolhead cover

## 2025-01-29

- added fan and pcb to toolhead assembly
- updated toolhead

## 2025-01-27

- fixed BOM typo [#1](https://github.com/kemsky/creality-k1-xy-rails-mod/issues/1)

## 2025-01-14

- added side fan duct

## 2024-12-26

- updated rail mounts to reduce Y vibrations

## 2024-12-11

- initial commit

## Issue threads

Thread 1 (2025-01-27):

front idler screws typo ?

ParadoxGopher, 2025-01-27:
you are listing `DIN 912 Flat Head Cap Screw M4x30` for the front idlers
should it be `DIN 7991` or `Socket Head Cap Screw` ?

I am currently creating a shopping list in case you are interested I can submit it in a PR

kemsky, 2025-01-27:
> I am currently creating a shopping list in case you are interested I can submit it in a PR

You can add it to this ticket or submit a PR

Closed 2025-01-27.

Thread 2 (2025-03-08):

K-1 SE

serbiansky, 2025-03-08:
Is it possible to print the parts in PETG as I do not have closed printer for other materials?

kemsky, 2025-03-08:
@serbiansky, no, temperature inside printer is too high for PETG, toolhead will get too hot 100%. It is easy to create temporary enclosure for you printer, for example you can cut panels from cardboard.

Closed 2025-03-10.

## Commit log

2024-12-18 update documentation
    [cad_M4_DIN912_30mm.FCStd, cad_nema17_42_48.FCStd, k1_front_idler_left.FCStd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]
2024-12-18 automate screenshots
    [cad_M4_DIN912_20mm.FCStd, cad_M4_DIN912_30mm.FCStd, cad_m4_35mm.FCStd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]
2024-12-18 add screenshots
    [k1_camera.FCStd, k1_camera.stl]
2024-12-19 update assembly
2024-12-25 updated rail mounts
    [cad_assembly.FCStd, k1_rail_mount.FCStd, k1_rail_mount.step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]
2025-01-06 update cable covers, remove some experimental models
2025-01-06 update cable covers
    [k1_cable_cover_vertical_bottom.FCStd, k1_cable_cover_vertical_bottom.step, k1_cable_cover_vertical_bottom.stl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]
2025-01-09 add bonus models
    [k1_toolhead_experimental.FCStd]
2025-01-14 uniform style
    [k1_cable_cover_horizontal.FCStd, k1_cable_cover_horizontal.step, k1_cable_cover_horizontal.stl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]
2025-01-14 add side fan duct
    [k1_side_fan_duct.FCStd, k1_side_fan_duct.step, k1_side_fan_duct.stl]
2025-01-15 side fan
    [k1_side_fan_duct.FCStd, k1_side_fan_duct.step, k1_side_fan_duct.stl]
2025-01-22 update toolhead
    [k1_rail_pad_fysetc.FCStd, k1_rail_pad_fysetc.step, k1_rail_pad_fysetc.stl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]
2025-02-04 add compact toolhead cover
    [k1_toolhead_cover_experimental.FCStd, k1_toolhead_cover_experimental.step, k1_toolhead_cover_experimental.stl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]
2025-02-08 update compact toolhead cover
    [k1_toolhead_cover_experimental.step, k1_toolhead_cover_experimental.stl]
2025-03-04 update experimental cover, toolhead
    [k1_toolhead_cover_experimental.step, k1_toolhead_experimental.FCStd, tool_mgn5_bracket_experimental.FCStd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]
2025-03-25 update experimental toolhead
    [k1_toolhead_cover_experimental.FCStd, k1_toolhead_cover_experimental.step]
2025-04-04 update joints
    [k1_joint_left.FCStd, k1_joint_left.step, k1_joint_left.stl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]
2025-04-06 simplify clamps printing
    [k1_toolhead_left_clamp.FCStd, k1_toolhead_left_clamp.step, k1_toolhead_left_clamp.stl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]
2025-04-19 make toolhead compatible with extruder from Creality CFS kit
    [k1_toolhead.FCStd, k1_toolhead.step, k1_toolhead.stl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]
2025-05-03 prepare motor mounts and toolhead for cfs
    [k1_motor_mount_left.FCStd, k1_motor_mount_left.step, k1_motor_mount_left.stl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]
2025-05-03 add cutter block
    [k1_cutter_block.FCStd, k1_cutter_block.step, k1_cutter_block.stl]
2025-05-28 correct rails size
2025-05-31 added initial version of hopper
    [k1_hopper.FCStd, k1_hopper.step, k1_hopper.stl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]
2025-05-31 updated joints, motor mounts
    [k1_joint_left.FCStd, k1_joint_left.step, k1_joint_left.stl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]
2025-06-27 add belts tuning info
2025-06-27 add BIQU Microprobe
    [k1_hopper.FCStd, k1_hopper.step, k1_hopper.stl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]
2025-06-28 add printing orientation
2025-09-02 correct tensioners size, add microprobe fix
    [k1_tensioner_left.FCStd, k1_tensioner_right.FCStd, k1_tensioner_right.step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]
2026-01-15 correct BOM
